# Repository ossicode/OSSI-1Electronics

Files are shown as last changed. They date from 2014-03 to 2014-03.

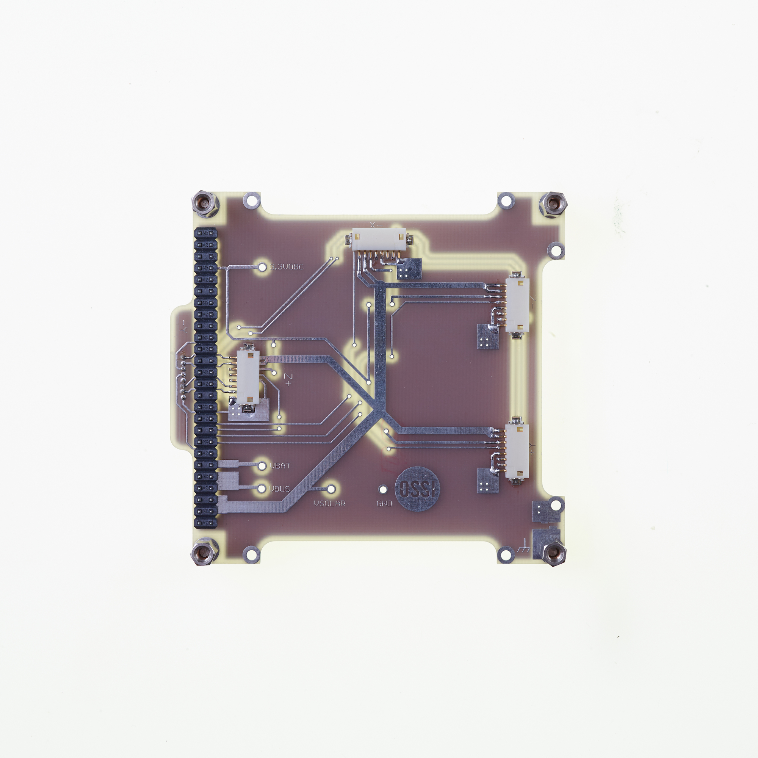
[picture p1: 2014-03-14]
OSSI-1 Interface Board/image/interface_T.jpg

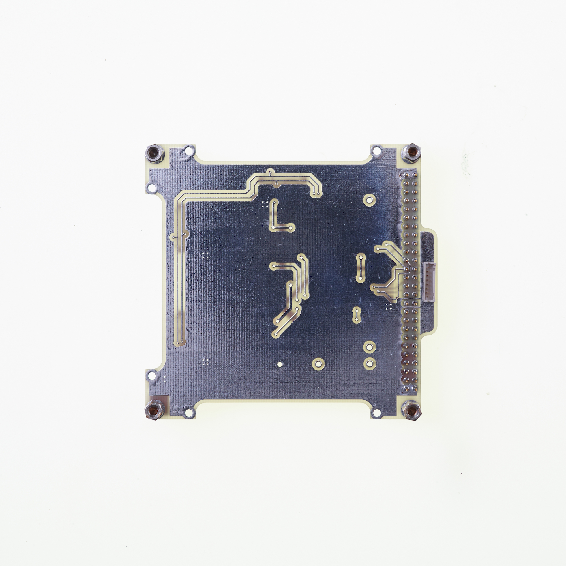
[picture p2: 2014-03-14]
OSSI-1 Interface Board/image/interface_B.jpeg

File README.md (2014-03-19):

### OSSI-1 Satellite Electronics Final Version 
#### Launched on 19th April 2013

**Check for modules for images, schematics, and BOMs.**

Mainly Eagle 6.1 / 6.5 version  
Please, see the comments from the schematic file for more information.  
Block diagram and rationale behind the design will be provided with video turorial soon.  

Open Source Satellite Initiative http://opensat.cc

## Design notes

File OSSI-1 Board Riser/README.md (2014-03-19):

### OSSI-1 Satellite Baord Riser

**Riser board to connect the signals between the battery board and the LED controller**

Mainly Eagle 6.1 / 6.5 version  
Please, see the comments from the schematic file for more information.  
Block diagram and rationale behind the design will be provided with video turorial soon.  

Open Source Satellite Initiative http://opensat.cc



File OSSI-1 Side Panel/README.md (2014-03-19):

### OSSI-1 Side Panel

**Solar panel for the sides.**  
**Temperature & current sensors are mounted on the panel for monitoring.**

Mainly Eagle 6.1 / 6.5 version  
Please, see the comments from the schematic file for more information.  
Block diagram and rationale behind the design will be provided with video turorial soon.  

Open Source Satellite Initiative http://opensat.cc



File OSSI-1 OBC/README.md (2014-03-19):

### OSSI-1 Satellite OBC Module

**The OBC is the mainboard of the satellite.**  
**The board checks the status of the satellite and makes decisions based on the data.**

Mainly Eagle 6.1 / 6.5 version  
Please, see the comments from the schematic file for more information.  
Block diagram and rationale behind the design will be provided with video turorial soon.  

Open Source Satellite Initiative http://opensat.cc



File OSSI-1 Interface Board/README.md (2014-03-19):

### OSSI-1 Satellite Interface Board

**The interface board is used to connect all solar paneles and deliver the power to the EPS.**  
**As the board is the the on the top, some signals can be measured for inspection.**

Mainly Eagle 6.1 / 6.5 version  
Please, see the comments from the schematic file for more information.  
Block diagram and rationale behind the design will be provided with video turorial soon.  

Open Source Satellite Initiative http://opensat.cc



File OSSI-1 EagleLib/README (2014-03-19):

Open Source Satellite Initiative Eagle CAD Library
http://opensat.cc

We used Eagle CAD 6.1 to design the board. Please, download one from:
http://www.cadsoftusa.com/downloads/

OSSI.lbr is the last version.

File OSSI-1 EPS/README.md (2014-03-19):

### OSSI-1 Satellite EPS

**EPS is the power supply board for the satellite.** 
**Multiple power sources are OR-ed by ideal diodes for reliabilty.**

Mainly Eagle 6.1 / 6.5 version  
Please, see the comments from the schematic file for more information.  
Block diagram and rationale behind the design will be provided with video turorial soon.  

Open Source Satellite Initiative http://opensat.cc



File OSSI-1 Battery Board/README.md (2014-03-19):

### OSSI-1 Satellite Battery Board

**The battery board contains Saft 144350 lithium-ion battery and two Nesscap supercapacitors.**  
**2 analog out temperature modules are attached to the battery and the supercapacitor for temp. monitoring.**

Mainly Eagle 6.1 / 6.5 version  
Please, see the comments from the schematic file for more information.  
Block diagram and rationale behind the design will be provided with video turorial soon.  

Open Source Satellite Initiative http://opensat.cc



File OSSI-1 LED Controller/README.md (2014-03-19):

### OSSI-1 Satellite LED Controller Module

**LED Controller Module is responsible for controlling 44W high power LEDs powered from supercapacitors.**  

Mainly Eagle 6.1 / 6.5 version  
Please, see the comments from the schematic file for more information.  
Block diagram and rationale behind the design will be provided with video turorial soon.  

Open Source Satellite Initiative http://opensat.cc



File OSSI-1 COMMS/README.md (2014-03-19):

### OSSI-1 Satellite COMMS

**Main communication system in OSSI-1.**  
**UHF RX/TX and TX is off by default to abide by the international rules.**

Mainly Eagle 6.1 / 6.5 version  
Please, see the comments from the schematic file for more information.  
Block diagram and rationale behind the design will be provided with video turorial soon.  

Open Source Satellite Initiative http://opensat.cc



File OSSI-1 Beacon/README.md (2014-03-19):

### OSSI-1 Satellite Beacon

**Beacon outputs 100mW VHF signas to transmit OSSI-1 satellite health data.**  
**Beacon transmits continuously.**

Mainly Eagle 6.1 / 6.5 version  
Please, see the comments from the schematic file for more information.  
Block diagram and rationale behind the design will be provided with video turorial soon.  

Open Source Satellite Initiative http://opensat.cc



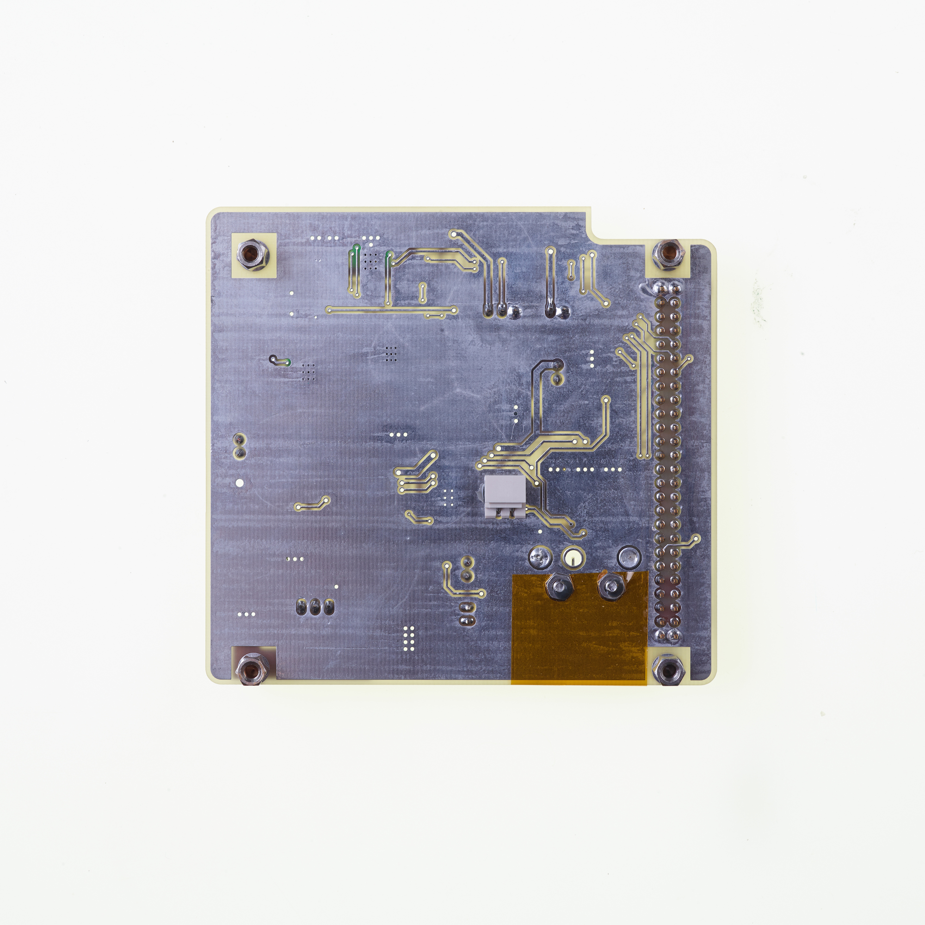
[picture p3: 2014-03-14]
OSSI-1 EPS/image/EPS_B.jpg

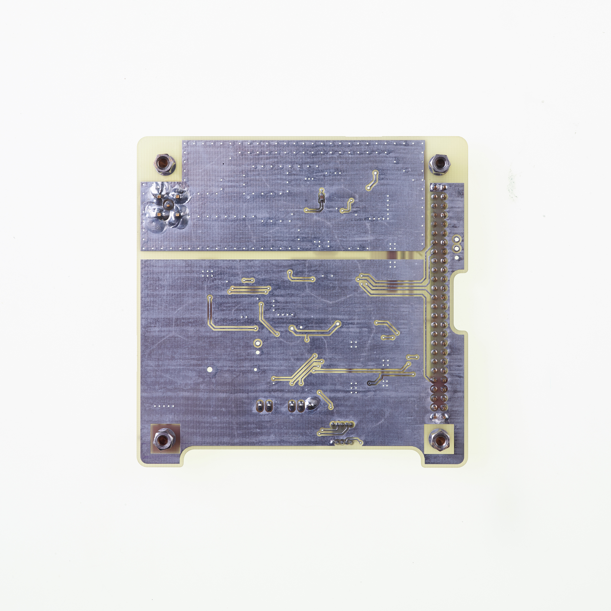
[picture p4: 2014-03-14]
OSSI-1 Beacon/image/Beacon_B.jpg

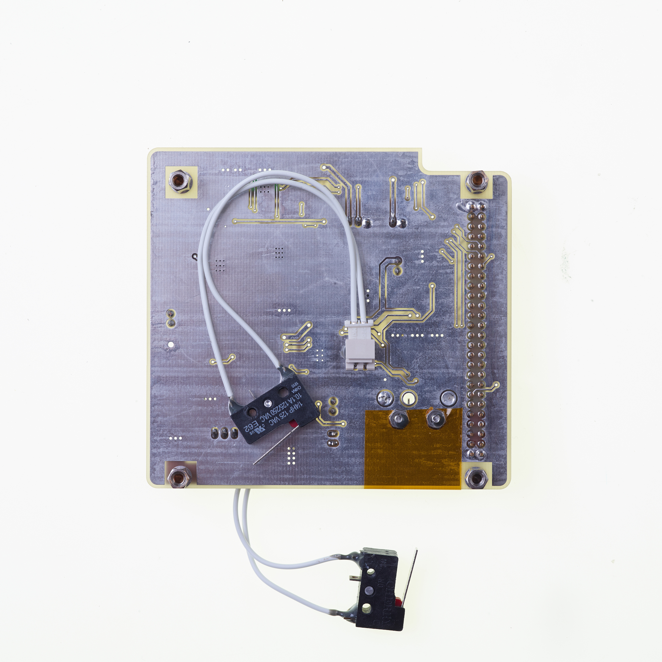
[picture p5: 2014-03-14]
OSSI-1 EPS/image/EPS_Switch_B.jpg

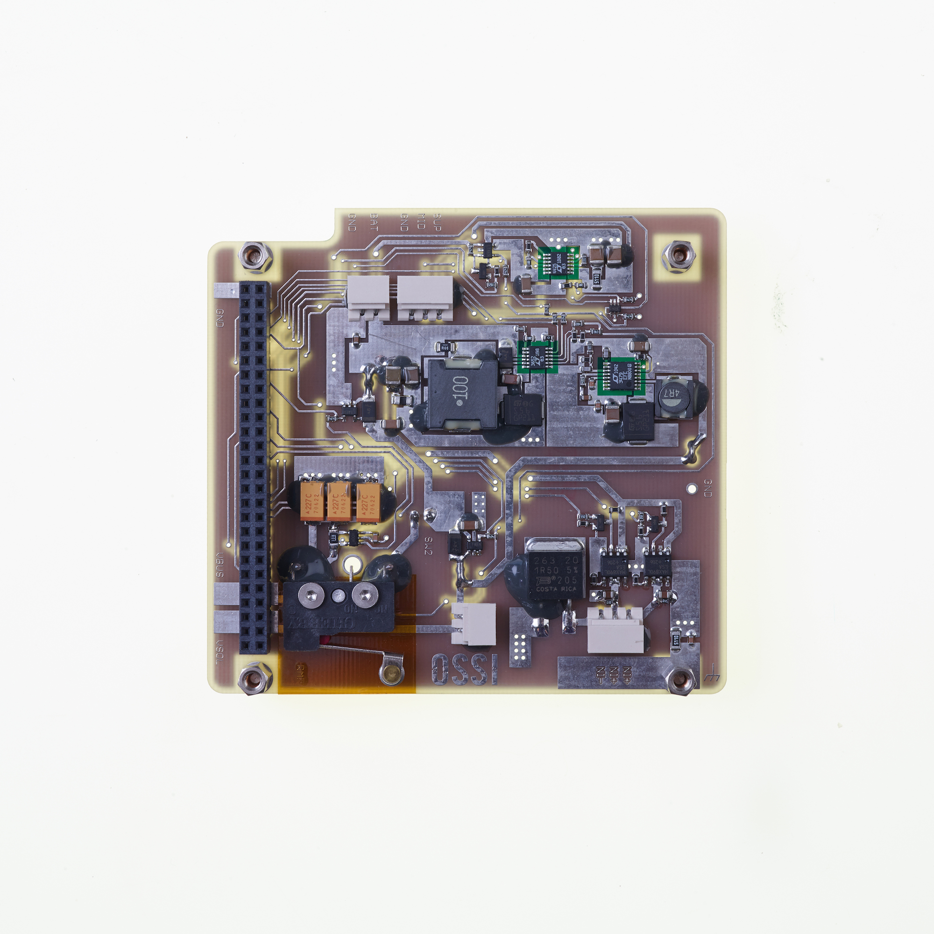
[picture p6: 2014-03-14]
OSSI-1 EPS/image/EPS_T.jpg

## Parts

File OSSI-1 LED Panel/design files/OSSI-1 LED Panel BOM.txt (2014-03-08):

Part	Value	Attributes	Package	Description	Part Num
LED1	LED-P7		P7		*
LED2	LED-P7		P7		*
LED3	LED-P7		P7		*
LED4	LED-P7		P7		*
X1	P-PAD		P-PAD		*
X2	P-PAD		P-PAD		*

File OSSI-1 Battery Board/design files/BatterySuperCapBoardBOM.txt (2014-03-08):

Part	Value	Attributes	Package	Description	Part Num
H1	MOUNT-PAD-ROUND3.2		3.2-PAD-ROUND		*
H2	MOUNT-PAD-ROUND3.2		3.2-PAD-ROUND		*
H3	MOUNT-PAD-ROUND3.2		3.2-PAD-ROUND		*
H4	MOUNT-PAD-ROUND3.2		3.2-PAD-ROUND		*
H5	MOUNT-PAD-ROUND3.2		3.2-PAD-ROUND		*
H6	MOUNT-PAD-ROUND3.2		3.2-PAD-ROUND		*
H7	MOUNT-PAD-ROUND3.2		3.2-PAD-ROUND		*
H8	MOUNT-PAD-ROUND3.2		3.2-PAD-ROUND		*
H9	MOUNT-PAD-ROUND3.2		3.2-PAD-ROUND		*
H10	MOUNT-PAD-ROUND3.2		3.2-PAD-ROUND		*
H11	MOUNT-PAD-ROUND3.2		3.2-PAD-ROUND		*
H12	MOUNT-PAD-ROUND3.2		3.2-PAD-ROUND		*
H13	MOUNT-PAD-ROUND3.2		3.2-PAD-ROUND		*
H14	MOUNT-PAD-ROUND3.2		3.2-PAD-ROUND		*
H15	MOUNT-PAD-ROUND3.2		3.2-PAD-ROUND		*
H16	MOUNT-PAD-ROUND3.2		3.2-PAD-ROUND		*
X1	ESQ-126-38-G-D		ESQ-126-XX-X-D	Samtec ESQ-126-XX-G-D Elevated Sockets Seires	*
X2	WEIDMULLER		WEIDMULLER1760490000		*
X3			1X03	Header 3	*
X4			1X03	Header 3	*

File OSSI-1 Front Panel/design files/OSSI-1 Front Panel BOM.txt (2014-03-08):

Part	Value	Attributes	Package	Description	Part Num
ADS1	OSSIADS		OSSIADS		*
C1	5.975pF		C0805(2012)		*
C2	5.975pF		C0805(2012)		*
L1	22.4nH		L0805(2012)		*
L2	22.4nH		L0805(2012)		*
L3	6mm dia, 5 turn		0207/10	INDUCTOR, American symbol	*
LD1	TEMT6000X01		TEMT6000-SEN	Ambient Light Sensor	*
R1	10k		R0805(2012)		*
X1	RFCON-MCX-V		MCX-V	RF Connectors	*
X2	RFCON-MCX-V		MCX-V	RF Connectors	*
X3	P-PAD-S		P-PAD-S		*
X4	P-PAD-S		P-PAD-S		*
X5	P-PAD-S		P-PAD-S		*
X6	P-PAD		P-PAD		*
X7	P-PAD		P-PAD		*
X8	P-PAD		P-PAD		*
X9	P-PAD		P-PAD		*
X10	P-PAD		P-PAD		*
X11	P-PAD-S		P-PAD-S		*

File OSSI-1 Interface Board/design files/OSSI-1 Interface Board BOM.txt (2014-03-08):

Part	Value	Attributes	Package	Description	Part Num
TP1	TP		TP-13		*
TP2	TP		TP-13		*
TP3	TP		TP-13		*
TP4	TP		TP-13		*
TP5	TP		TP-13		*
U$1	OSSILOGO-10		OSSILOGO1010		*
X1	ESQ-126-38-G-D		ESQ-126-XX-X-D	Samtec ESQ-126-XX-G-D Elevated Sockets Seires	*
C43	DNP		C0805(2012)		*
H1	MOUNT-PAD-ROUND3.2		3.2-PAD-ROUND		*
H2	MOUNT-PAD-ROUND3.2		3.2-PAD-ROUND		*
H3	MOUNT-PAD-ROUND3.2		3.2-PAD-ROUND		*
H4	MOUNT-PAD-ROUND3.2		3.2-PAD-ROUND		*
H5	MOUNT-PAD-ROUND2.1		2.1-PAD-ROUND		*
H6	MOUNT-PAD-ROUND2.1		2.1-PAD-ROUND		*
H9	MOUNT-PAD-ROUND2.1		2.1-PAD-ROUND		*
H10	MOUNT-PAD-ROUND2.1		2.1-PAD-ROUND		*
H11	MOUNT-PAD-ROUND2.1		2.1-PAD-ROUND		*
H12	MOUNT-PAD-ROUND2.1		2.1-PAD-ROUND		*
R39	DNP		WSL1206		*
X3	DF13DF13A-8P-1.25H		DF13A-8P	Hirose DF13 series connector	*
X4	DF13DF13-8P-1.25DSA		DF13-8P-1.25DSA	Hirose DF13 series connector	*
X6	DF13DF13A-8P-1.25H		DF13A-8P	Hirose DF13 series connector	*
X7	DF13DF13A-8P-1.25H		DF13A-8P	Hirose DF13 series connector	*
X8	DF13DF13A-8P-1.25H		DF13A-8P	Hirose DF13 series connector	*

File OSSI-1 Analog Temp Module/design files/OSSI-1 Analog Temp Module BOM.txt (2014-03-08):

Part	Value	Attributes	Package	Description	Part Num
C1	100nF		C0603(1608)		*
C2	100nF		C0603(1608)		*
JP1	JP2		JP2SMD0603		*
JP2	JP2		JP2SMD0603		*
U1	LM94022		SC70-5	LM94022 Temp Sensor From TI	*
X1	P-PAD-S		P-PAD-S		*
X2	P-PAD-S		P-PAD-S		*
X3	P-PAD-S		P-PAD-S		*

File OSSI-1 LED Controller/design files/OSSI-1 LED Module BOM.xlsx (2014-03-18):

Part | Value | Package | Description | Note | Manufacturer | Part Num | Order
C1 | DNP | C0805(2012)
H1 | MOUNT-PAD-ROUND3.2 | 3.2-PAD-ROUND
H2 | MOUNT-PAD-ROUND3.2 | 3.2-PAD-ROUND
H3 | MOUNT-PAD-ROUND3.2 | 3.2-PAD-ROUND
H4 | MOUNT-PAD-ROUND3.2 | 3.2-PAD-ROUND
R1 | DNP | WSL1206
X1 | ESQ-126-38-G-D | ESQ-126-XX-X-D | Samtec ESQ-126-XX-G-D Elevated Sockets Seires | Used by many satellites | Samtec | ESQ-126-38-G-D | Samtec.com
C2 | 12.5pF | C0603(1608)
C3 | 100nF | C0603(1608)
C4 | 12.5pF | C0603(1608)
C5 | 100nF | C0603(1608)
C6 | 100nF | C0603(1608)
C7 | 100nF | C0603(1608)
C8 | 100nF | C0603(1608)
C9 | 10uF, LDO Tantal 16V | C1206(3216)-A | TAJA105M020RNJ | Tantal Capacitor for LDO | Vishay Sprague | TR3A106K016C1700 | Digikey.com
C10 | 10uF, LDO Tantal 16V | C1206(3216)-A | TAJA105M020RNJ | Tantal Capacitor for LDO | Vishay Sprague | TR3A106K016C1700 | Digikey.com
C11 | 4.7uF, 1206 Cap | C1206-GCM31
C12 | 1uF | C0603(1608)
C13 | 100nF | C0603(1608)
C14 | 10uF, LDO Tantal 16V | C1206(3216)-A | TAJA105M020RNJ | Tantal Capacitor for LDO | Vishay Sprague | TR3A106K016C1700 | Digikey.com
C15 | 1uF 0805 | C0805(2012) |  | 35V, X7R | Murata | GCM21BR7YA105KA55L | Digikey.com
JP1 |  | JP1 | JUMPER
JP2 |  | JP1 | JUMPER
LED1 |  | LED-0603 | LEDs
LED2 |  | CHIPLED_0603 | LED
Q1 | NX-3215 | NX-3215 | NDK 32.768 kHz SMD Crystal | Automotive Grade | NDK | NX3215SA-32.768K-STD-MUS-2 | Digikey.com
R2 | 250 | R0603(1608)
R3 | 10k | R0603(1608)
R4 | 1k | R0603(1608)
R5 | 250 | R0603(1608)
R6 | 10k | R0603(1608)
R7 | 4.7k | R0603(1608)
R8 | 4.7k | R0603(1608)
R9 | 3k | R0603(1608)
R10 | 1k | R0603(1608)
R11 | 5.1k | R0603(1608)
R12 | 1k | R0603(1608)
R13 | 4.7k | R0603(1608)
R14 | 47k | R0603(1608)
R15 | 100k | R0603(1608)
R16 | DNP | R0603(1608)
R17 | 1k | R0603(1608)
R18 | 1.5k | R0603(1608)
R19 | 2.4k | R0603(1608)
R20 | 100k | R0603(1608)
R21 | 0.005, 2W RSENSE | R4527(12070) |  | High Power (2W) 1% Current Sense Resistor | Vishay Dale | WSR25L000FEA | element14.com
R22 | 1.1k | R0603(1608)
R23 | 1k | R0603(1608)
R24 | 100k | R0603(1608)
R25 | DNP | R0603(1608)
R26 | 1.5k | R0603(1608)
R27 | 0 | R0603(1608)
R28 | TBD | R0603(1608)
R29 | 100k | R0603(1608)
R30 | 100k | R0603(1608)
TP1 | TP | TP-13
TP2 | TP | TP-13
TP3 | TP | TP-13
TP4 | TP | TP-13
TP5 | TP | TP-13
TP6 | TP | TP-13
TP7 | TP | TP-13
TR1 | FDV301N | SOT23 | FDV301N Digital N channel - FET | Used sucessfully by swisscube | Fairchild Semiconductor | FDV301N | Digikey.com
TR2 | FDD8896 | TO252 | FDD8896 | 30V 94A N-Ch Mosfet for 9A pulse LED driving | Fairchild Semiconductor | FDD8896 | Digikey.com
U$ | OSSILOGORECT | OSSILOGORECT1005
U1 | MSP430F2132 | PW28 | *** MSP430F21x2 *** PW28 | high current rating | Texas Instruements | MSP430F2132TPWR | Digikey.com
U2 | OPA2347 | SOT23-8DCN | OPA2347 | op-amp | Texas Instruements | OPA2347EA/250 | Digikey.com
U3 | MAX4376 | SOT23-5DBV |  | Current Sensor, Gain = 50 | Maxim IC | MAX4376FAUK+T | Digikey.com
U4 | LM7321 | SO8 | LM7321 | op-amp used as mosfet driver | Texas Instruements | LM7321MA/NOPB | element14.com
U5 | MAX1682 | SOT23-5DBV | MAX1682EUK+T Charge Pump | Charge pump for lm7321 power | Maxim IC | MAX1682EUK+T | Digikey.com
U6 | TPS3838 | SOT23-5DBV | TPS3838 | IC Supervisor for relaible power-on | Texas Instruements | TPS3838K33QDBVRQ1 | Digikey.com
U7 | MAX890L | SO8 | MAX 890L | Current Limiter for SEU / SEL | Maxim IC | MAX890LESA+ | Digikey.com
U8 | MCP1700_SOT23 | SOT23 | MCP1700 LDO from Microchips | LDO used successfully by cubesats / External Capacitor is not that important compared to other LDO | Microchip | MCP1700T-3302E/TT | Digikey.com
X2 | 5268-03 | 5268-03
X3 |  | 1X03 | Header 3
X4 | 5268-03 | 5268-03
X5 | JTAG10PINMINI-H | M50-3200545 |  | Mini right angle 10-pin JTAG for MSP430 | Harwin Inc | M50-3200545 | Digikey.com
X6 | ICCON_POWERCON | ICCON6643220-1 |  | 35A rated power connector for led power | TE Connectivity | 6643220-1
X7 | ICCON_POWERCON | ICCON6643220-1 |  | 35A rated power connector for led power | TE Connectivity | 6643220-1
X8 | WEIDMULLER | WEIDMULLER1760490000 |  | 15A rated connector for led connection | Weidmuller | 1760490000
Unless noted othersie,_x000a_- Capacitors: GCM series from Murata / CGA series from TDK_x000a_- Resistors: ERJ 1% or 5% series from Panasonic Electronic Components_x000a__x000a_All all can be purchased from Digikey.com

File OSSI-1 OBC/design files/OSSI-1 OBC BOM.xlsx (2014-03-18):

Part | Value | Package | Description | Note | Manufacturer | Part Num | Order
H1 | MOUNT-PAD-ROUND3.2 | 3.2-PAD-ROUND
H2 | MOUNT-PAD-ROUND3.2 | 3.2-PAD-ROUND
H3 | MOUNT-PAD-ROUND3.2 | 3.2-PAD-ROUND
H4 | MOUNT-PAD-ROUND3.2 | 3.2-PAD-ROUND
X1 | ESQ-126-38-G-D | ESQ-126-XX-X-D | Samtec ESQ-126-XX-G-D Elevated Sockets Seires | Used by many satellites | Samtec | ESQ-126-37-G-D | Samtec.com
C1 | 100nF | C0603(1608)
C2 | 100nF | C0603(1608)
C3 | 100nF | C0603(1608)
C4 | 100nF | C0603(1608)
C5 | 100nF | C0603(1608)
C6 | 100nF | C0603(1608)
C7 | 100nF | C0603(1608)
C8 | 100nF | C0603(1608)
C9 | 100nF | C0603(1608)
C10 | 100nF | C0603(1608)
C11 | 100nF | C0603(1608)
C12 | 100nF | C0603(1608)
C13 | 100nF | C0603(1608)
C14 | 100nF | C0603(1608)
C15 | 100nF | C0603(1608)
C16 | 100nF | C0603(1608)
C17 | 100nF | C0603(1608)
R1 | 10k | R0603(1608)
R2 | 10k | R0603(1608)
R3 | 10k | R0603(1608)
R4 | 10k | R0603(1608)
R5 | 10k | R0603(1608)
R6 | 10k | R0603(1608)
R7 | 10k | R0603(1608)
R8 | 10k | R0603(1608)
R9 | 10k | R0603(1608)
R10 | 100k | R0603(1608)
R11 | 100k | R0603(1608)
R12 | 100k | R0603(1608)
R13 | 100k | R0603(1608)
R14 | 100k | R0603(1608)
R15 | 100k | R0603(1608)
R16 | 100k | R0603(1608)
R17 | 100k | R0603(1608)
R18 | 10k | R0603(1608)
U1 | OPA4347 | TSSOP14-PW | OPA4347 | op-amp | Texas Instruements | OPA4347EA/250 | Digikey.com
U2 | ADG708 | TSSOP16-RU |  | analog mux | Analog devices | ADG708CRUZ | Digikey.com
U3 | OPA4347 | TSSOP14-PW | OPA4347 | op-amp | Texas Instruements | OPA4347EA/250 | Digikey.com
U4 | ADR121 | TSOT-6UJ-6 | ADR127 | 2.5V reference | Analog devices | ADR121AUJZ-R2 | element14.com
U5 | ADG708 | TSSOP16-RU |  | analog mux | Analog devices | ADG708CRUZ | Digikey.com
U6 | OPA4347 | TSSOP14-PW | OPA4347 | op-amp | Texas Instruements | OPA4347EA/250 | Digikey.com
BAT1 | BATTERY-BH32T | BH32T-C-G |  | CR2032 battery holder | MPD (Memory Protection Devices) | BH32T-C-G | Digikey.com
C18 | 100nF | C0603(1608)
C19 | 100nF | C0603(1608)
C20 | 1uF 0805 | C0805(2012) |  | 35V, X7R | Murata | GCM21BR7YA105KA55L | Digikey.com
C21 | 100nF | C0603(1608)
C22 | 1uF 0805 | C0805(2012) |  | 35V, X7R | Murata | GCM21BR7YA105KA55L | Digikey.com
C23 | 1uF 0805 | C0805(2012) |  | 35V, X7R | Murata | GCM21BR7YA105KA55L | Digikey.com
C24 | 100nF | C0603(1608)
C25 | 100nF | C0603(1608)
C26 | 100nF | C0603(1608)
C27 | 100nF | C0603(1608)
C28 | 100nF | C0603(1608)
C29 | 4.7uF, 1210 | C1206-GCM31 |  | Ceramic 25V, X7R | Murata | GCM31CR71E475KA55L | Digikey.com
C30 | 10uF,3225 | C1210-GCM32 |  | 25V, X7R | Murata | GCM32ER71E106KA57L | Digikey.com
D1 | MMSD4148T1G | SOD-123 |  | switching diode for gyro | On Semi | MMSD4148T1G | Mouser.com
F1 | POLYSWITCH | NANOSMDC150FCT | Resettable Polyswitch | 1.5A Resettable Polyswitch fuse | TE Connectivity | NANOSMDC150F-2 | Digikey.com
L1 | 470uH, 240mA | L(2220) |  | inductor for gyro | Murata | LQH55DN471M03L | Mouser.com
R19 | 250 | R0603(1608)
R20 | 470k | R0603(1608)
R21 | 250 | R0603(1608)
R22 | 1.5k | R0603(1608)
R23 | 1.5k | R0603(1608)
R24 | 250 | R0603(1608)
R25 | 250 | R0603(1608)
R26 | 1.5k | R0603(1608)
R27 | 100k | R0603(1608)
R28 | 1.5k | R0603(1608)
R29 | 1.5k | R0603(1608)
R30 | 250 | R0603(1608)
R31 | 250 | R0603(1608)
R32 | 4.7k | R0603(1608)
R33 | 470k | R0603(1608)
R34 | 470k | R0603(1608)
R35 | 33k | R0603(1608)
R36 | 4.7k | R0603(1608)
R37 | 120, DNP | R0603(1608)
R38 | 250 | R0603(1608)
R39 | 4.7k | R0603(1608)
R40 | 33k | R0603(1608)
R41 | 250 | R0603(1608)
R42 | 4.7k | R0603(1608)
R43 | 470k | R0603(1608)
R44 | 4.7k | R0603(1608)
R45 | 100k | R0603(1608)
R46 | 470k | R0603(1608)
R47 | 100k | R0603(1608)
R48 | 100k | R0603(1608)
R49 | 100k | R0603(1608)
R50 | 1.5k | R0603(1608)
R51 | 1.5k | R0603(1608)
R52 | 1.5k | R0603(1608)
R53 | 1.5k | R0603(1608)
R54 | 10k | R0603(1608)
R55 | 1.5k | R0603(1608)
R56 | 1.5k | R0603(1608)
R57 | 1.5k | R0603(1608)
R58 | 10k | R0603(1608)
R59 | 10k | R0603(1608)
R60 | 10k | R0603(1608)
R61 | 10k | R0603(1608)
R62 | 100k | R0603(1608)
TR1 | FDV301N | SOT23 | FDV301N Digital N channel - FET | Used sucessfully by swisscube | Fairchild Semiconductor | FDV301N | Digikey.com
U7 | DS3231-L | SO16L | DS3231 | RTC | Maxim IC | DS3231SN# | element14.com
U8 | 24LC256-8LEAD | SO08-208 | 24LC256 | EEPROM | Microchip | 24LC256-E/SM | Mouser.com
U9 | LTC4411 | TSOT23-5 | Linear Techonology LTC4411 ideal diode | To power reset i2c ICs on OBC | Linear Technology | LTC4411ES5#TRMPBF | element14.com
U10 | ADXRS450SOIC | SOIC-16CAV |  | Gyro | Analog devices | ADXRS450BRGZ | Digikey.com
U11 | FM24V02-G | SO8 | FM24V02 | F-Ram | Ramtron | FM24V02-G | Mouser.com
U12 | TMP101 | SOT23-6DBV | TMP101 Digital Temerature Sensor with I2C Interface from Texas Instruments with Alert Function | i2c temp sensor with alarm | Texas Instruements | TMP101NA/3K | Digikey.com
U13 | SN65HVD11QD | SO8 | SN65HVD11 3.3V RS485 Transceiver | external interface | Texas Instruements | SN65HVD11QD | Mouser.com
U14 | TCA9548APWR | TSSOP-24-PW | TCA9548APWR | I2C switch | Texas Instruements | TCA9548APWR | Digikey.com
U15 | SN74LVC8T245PWR | PW_R-PDSO-G24 | SN74LVC8T245 | io protection buffer | Texas Instruements | SN74LVC8T245PWR | Mouser.com
U16 | LTC4411 | TSOT23-5 | Linear Techonology LTC4411 ideal diode | To bypass external power to satellite | Linear Technology | LTC4411ES5#TRMPBF | element14.com
X2 | MOLEX-22-05-7045 | 22-05-7045 | molex spoxt 5268 series 22-05-7045 for external interface
C31 | 12.5pF | C0603(1608)
C32 | 12.5pF | C0603(1608)
C33 | 100nF | C0603(1608)
C34 | 100nF | C0603(1608)
C35 | 100nF | C0603(1608)
C36 | 100nF | C0603(1608)
C37 | 100nF | C0603(1608)
C38 | 1uF | C0603(1608)
C39 | 100nF | C0603(1608)
C40 | 10uF, LDO Tantal 16V | C1206(3216)-A | TAJA105M020RNJ | Tantal Capacitor for LDO | Vishay Sprague | TR3A106K016C1700 | Digikey.com
C41 | 10uF, LDO Tantal 16V | C1206(3216)-A | TAJA105M020RNJ | Tantal Capacitor for LDO | Vishay Sprague | TR3A106K016C1700 | Digikey.com
JP1 |  | JP1 | JUMPER
LED1 |  | LED-0603 | LEDs
Q1 | NX-3215 | NX-3215 | NDK 32.768 kHz SMD Crystal | Automotive Grade | NDK | NX3215SA-32.768K-STD-MUS-2 | Digikey.com
R63 | 250 | R0603(1608)
R64 | 250 | R0603(1608)
R65 | 10k | R0603(1608)
R66 | 300k | R0603(1608)
R67 | 10k | R0603(1608)
R68 | 4.7k | R0603(1608)
R69 | 4.7k | R0603(1608)
R70 | 4.7k | R0603(1608)
R71 | 4.7k | R0603(1608)
R72 | 0 | R0603(1608)
R73 | 0 | R0603(1608)
R74 | 6.2k | R0603(1608)
R75 | 0 | R0603(1608)
R76 | 100k | R0603(1608)
R77 | 100k | R0603(1608)
U$1 | OSSILOGORECT | OSSILOGORECT1005
U17 | MSP430F1611 | PM/PAG64 | MSP430F1611 | Used by many cubesats / I2C issue in the chip / MSP430F2618 is better choice | Texas Instruements | MSP430F1611IPMR | Digikey.com
U18 | MAX6369 | SOT23-8 | MAX6369 | External Watchdog timer | Maxim IC | MAX6369KA+T | Digikey.com
U19 | TPS3838 | SOT23-5DBV | TPS3838 | IC Supervisor for relaible power-on | Texas Instruements | TPS3838K33QDBVRQ1 | Digikey.com
U20 | MAX890L | SO8 | MAX 890L | Current Limiter for SEU / SEL | Maxim IC | MAX890LESA+ | Digikey.com
U21 | MCP1700_SOT23 | SOT23 | MCP1700 LDO from Microchips | LDO used successfully by cubesats / External Capacitor is not that important compared to other LDO | Microchip | MCP1700T-3302E/TT | Digikey.com
X3 |  | 1X03 | Header 3
X4 | P-PAD-S | P-PAD-S
X5 | P-PAD-S | P-PAD-S
X6 | JTAG10PINMINI-H | M50-3200545 |  | Mini right angle 10-pin JTAG for MSP430 | Harwin Inc | M50-3200545 | Digikey.com
Unless noted othersie,_x000a_- Capacitors: GCM series from Murata / CGA series from TDK_x000a_- Resistors: ERJ 1% or 5% series from Panasonic Electronic Components_x000a__x000a_All all can be purchased from Digikey.com

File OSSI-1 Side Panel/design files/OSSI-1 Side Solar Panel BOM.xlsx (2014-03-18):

Part | Value | Package | Description | Note | Manufacturer | Part Num | Order
C1 | 100nF | C0603(1608)
D1 | STPS0520Z | SOD-123 | We use STPS0520Z by st.com diode for solar cell schottky diode. | schottky diode for reverse current blocking | STMicroelectronics | STPS0520Z | Digikey.com
D2 | STPS0520Z | SOD-123 | We use STPS0520Z by st.com diode for solar cell schottky diode.
D3 | STPS0520Z | SOD-123 | We use STPS0520Z by st.com diode for solar cell schottky diode.
D4 | STPS0520Z | SOD-123 | We use STPS0520Z by st.com diode for solar cell schottky diode.
D5 | STPS0520Z | SOD-123 | We use STPS0520Z by st.com diode for solar cell schottky diode.
D6 | STPS0520Z | SOD-123 | We use STPS0520Z by st.com diode for solar cell schottky diode.
D7 | STPS0520Z | SOD-123 | We use STPS0520Z by st.com diode for solar cell schottky diode.
D8 | STPS0520Z | SOD-123 | We use STPS0520Z by st.com diode for solar cell schottky diode.
D9 | STPS0520Z | SOD-123 | We use STPS0520Z by st.com diode for solar cell schottky diode.
D10 | STPS0520Z | SOD-123 | We use STPS0520Z by st.com diode for solar cell schottky diode.
D11 | STPS0520Z | SOD-123 | We use STPS0520Z by st.com diode for solar cell schottky diode.
D12 | STPS0520Z | SOD-123 | We use STPS0520Z by st.com diode for solar cell schottky diode.
H1 | MOUNT-PAD-ROUND2.1 | 2.1-PAD-ROUND
H2 | MOUNT-PAD-ROUND2.1 | 2.1-PAD-ROUND
H3 | MOUNT-PAD-ROUND2.1 | 2.1-PAD-ROUND
H4 | MOUNT-PAD-ROUND2.1 | 2.1-PAD-ROUND
JP1 | JP2 | JP2SMD0603 |  | set i2c address for tmp100
JP2 | JP2 | JP2SMD0603 |  | set i2c address for tmp100
R1 | 250 | R0603(1608)
R2 | 250 | R0603(1608)
R3 | 50m | WSL1206 |  | 1% current sense resistor | Vishay Dale | WSL1206R0500FEA18 | Digikey.com
R4 | 1k | R0603(1608)
S1 | TASCSOLARCELL | TASCSOLARCELL |  | Hard to get / Hard to mount / Used by many cubesats / Epo-Tek H20E silver epoxy is used for mounting | Spectrolab | TASC Solar Cell | spectrolab.com/‎
S2 | TASCSOLARCELL | TASCSOLARCELL
S3 | TASCSOLARCELL | TASCSOLARCELL
S4 | TASCSOLARCELL | TASCSOLARCELL
S5 | TASCSOLARCELL | TASCSOLARCELL
S6 | TASCSOLARCELL | TASCSOLARCELL
S7 | TASCSOLARCELL | TASCSOLARCELL
S8 | TASCSOLARCELL | TASCSOLARCELL
S9 | TASCSOLARCELL | TASCSOLARCELL
S10 | TASCSOLARCELL | TASCSOLARCELL
S11 | TASCSOLARCELL | TASCSOLARCELL
S12 | TASCSOLARCELL | TASCSOLARCELL
S13 | TASCSOLARCELL | TASCSOLARCELL
S14 | TASCSOLARCELL | TASCSOLARCELL
S15 | TASCSOLARCELL | TASCSOLARCELL
S16 | TASCSOLARCELL | TASCSOLARCELL
S17 | TASCSOLARCELL | TASCSOLARCELL
S18 | TASCSOLARCELL | TASCSOLARCELL
S19 | TASCSOLARCELL | TASCSOLARCELL
S20 | TASCSOLARCELL | TASCSOLARCELL
S21 | TASCSOLARCELL | TASCSOLARCELL
S22 | TASCSOLARCELL | TASCSOLARCELL
S23 | TASCSOLARCELL | TASCSOLARCELL
S24 | TASCSOLARCELL | TASCSOLARCELL
U$2 | OSSILOGO | OSSILOGORECT1005
U1 | TMP100 | SOT23-6DBV | TMP100 Digital Temerature Sensor with I2C Interface from Texas Instruments | I2C Temp sensor | Texas Instruements | TMP100NA/3K | Digikey.com
U2 | MAX4376 | SOT23-5DBV |  | Current Sensor, Gain = 50 | Maxim IC | MAX4376FAUK+T | Digikey.com
X1 | DF13DF13A-8P-1.25H | DF13A-8P | Hirose DF13 series connector | 1.25mm pitch |  | DF13A-8P-1.25H(50) | Digikey.com
Unless noted othersie,_x000a_- Capacitors: GCM series from Murata / CGA series from TDK_x000a_- Resistors: ERJ 1% or 5% series from Panasonic Electronic Components_x000a__x000a_All all can be purchased from Digikey.com

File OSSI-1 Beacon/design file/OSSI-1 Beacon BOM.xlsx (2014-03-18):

Part | Value | Package | Description | Note | Manufacturer | Part Num | Order
C1 | DNP | C0805(2012)
H1 | MOUNT-PAD-ROUND3.2 | 3.2-PAD-ROUND
H2 | MOUNT-PAD-ROUND3.2 | 3.2-PAD-ROUND
H3 | MOUNT-PAD-ROUND3.2 | 3.2-PAD-ROUND
H4 | MOUNT-PAD-ROUND3.2 | 3.2-PAD-ROUND
R1 | DNP | WSL1206
X1 | P-PAD-S | P-PAD-S
X2 | ESQ-126-38-G-D | ESQ-126-XX-X-D | Samtec ESQ-126-XX-G-D Elevated Sockets Seires | Used by many satellites | Samtec | ESQ-126-38-G-D | Samtec.com
X3 | P-PAD-S | P-PAD-S
C2 | 10nF | C0603(1608)
C3 | 10nF | C0603(1608)
C4 | 0R | C0603(1608)
C5 | 10nF | C0603(1608)
C6 | 100nF | C0603(1608)
C7 | 1uF,0805 | C0805(2012) |  | 35V, X7R | Murata | GCM21BR7YA105KA55L | Digikey.com
C8 | 22uF,1210 | C1210-GCM32 |  | Ceramic 25V, X7R | Taiyo Yuden | TMK325B7226MM-TR | Digikey.com
C9 | 1uF | C0603(1608)
C10 | 100nF | C0603(1608)
F1 | LFCN-160 | LFCN | LFCN-160 Low Pass Filter |  | Mini-Circuits | LFCN-160+ | http://www.minicircuits.com/
L1 | 470nH, 1008 size | L1008(2520) |  | Important for impedance matching | Coilcraft | 1008HT-R47TJL | Coilcraft.com
R2 | 100k | R0603(1608)
R3 | 6.2k | R0603(1608)
R4 | 100k | R0603(1608)
R5 | 100k | R0603(1608)
TR1 | FDV301N | SOT23 | FDV301N Digital N channel - FET | Used sucessfully by swisscube | Fairchild Semiconductor | FDV301N | Digikey.com
U1 | ADL5530 | LFCSP8_CP | ADL5530 |  | analog devices
U2 | MAX890L | SO8 | MAX 890L | Current Limiter for SEU / SEL | Maxim IC | MAX890LESA+ | Digikey.com
X4 | RFCON-MCX-R/A | MCX-R/A | RF Connectors
C11 | 22pF | C0603(1608) |  | RF Filter
C12 | 39pF | C0603(1608) |  | RF Filter
C13 | 22pF | C0603(1608) |  | RF Filter
C14 | 1nF | C0603(1608)
C15 | 10nF | C0603(1608)
C16 | 1nF | C0603(1608)
C17 | 2.2uF, 0805 | C0805(2012)
C18 | 100pF | C0603(1608)
C19 | 1uF | C0603(1608)
C20 | 1uF,0603 Too Small!! | C0603(1608)
C21 | DNP | C0603(1608)
C22 | 100pF | C0603(1608)
C23 | 1uF 0805 | C0805(2012)
C24 | 1uF,0603 | C0603(1608)
C25 | 22nF | C0603(1608)
C26 | 68pF | C0603(1608)
C27 | 1000pF | C0603(1608)
C28 | 22pF | C0603(1608)
L2 | 68nH | L0603(1608) |  | RF Filter | Coilcraft | 0603HP-68NXJLU | Coilcraft.com
L3 | 68nH | L0603(1608) |  | RF Filter | Coilcraft | 0603HP-68NXJLU | Coilcraft.com
L4 | 8.2nH | L0603(1608) |  | Very Important For PLL Lock, tune this value for more PLL lock margin | Coilcraft | 0603HP-8N2XJE | Coilcraft.com
L5 | 470nH, 1008 size | L1008(2520) |  | Important for impedance matching | Coilcraft | 1008HT-R47TJL | Coilcraft.com
R6 | 0 | R0603(1608)
R7 | 1M | R0603(1608)
R8 | 3.6k | R0603(1608)
R9 | 2.4k | R0603(1608)
R10 | 5.1k | R0603(1608)
TCXO1 | 19.2MHz | TCXO_M532 | 532L25DT19M2000: CTO electronic components Model 532 19.2MHz TCXO for RF transeiver |  | CTO electronic components | 532L25DT19M2000 | Digikey.com
U3 | NC7SZ04 | SC70-5 | UHS Inverter NC7SZ04 | To convert the output of TCXO from clipped sinewave to CMOS level | Fairchild | NC7SZ04P5X | Mouser.com
U4 | ADF7012 | TSSOP24 |  | Used successfully by many cubesats as VHF beacon / Hard to buy | analog devices | ADF7012BRUZ | element14.com
C29 | 100nF | C0603(1608)
C30 | TBD | C0603(1608)
C31 | 100nF | C0603(1608)
C32 | 12.5pF | C0603(1608)
C33 | 100nF | C0603(1608)
C34 | 12.5pF | C0603(1608)
C35 | 100nF | C0603(1608)
C36 | 100nF | C0603(1608)
C37 | 1uF | C0603(1608)
C38 | 100nF | C0603(1608)
C39 | 10uF, LDO Tantal 16V | C1206(3216)-A | TAJA105M020RNJ | Tantal Capacitor for LDO | Vishay Sprague | TR3A106K016C1700 | Digikey.com
C40 | 10uF, LDO Tantal 16V | C1206(3216)-A | TAJA105M020RNJ | Tantal Capacitor for LDO | Vishay Sprague | TR3A106K016C1700 | Digikey.com
C41 | 10nF | C0603(1608)
C42 | 22uF,1210 | C1210-GCM32 |  | Ceramic 25V, X7R | Taiyo Yuden | TMK325B7226MM-TR | Digikey.com
C43 | 100nF | C0603(1608)
D1 | BAT54S | SOT23 | Schottky Diodes | Switch ESD protection | STMicroelectronics | BAT54SFILM | Digikey.com
JP1 |  | JP1 | JUMPER
L6 | 7 R Ferrite Bead, 3A | L0805(2012) |  | 7 Ohm 3A Ferrite Bead for pi filter | Wurth Electronics Inc | 742792010 | Digikey.com
LED1 |  | LED-0603 | LEDs
Q1 | NX-3215 | NX-3215 | NDK 32.768 kHz SMD Crystal | Automotive Grade | NDK | NX3215SA-32.768K-STD-MUS-2 | Digikey.com
R11 | 47k | R0603(1608)
R12 | 4.7k | R0603(1608)
R13 | 250 | R0603(1608)
R14 | 10k | R0603(1608)
R15 | 1k | R0603(1608)
R16 | 250 | R0603(1608)
R17 | 100k | R0603(1608)
R18 | 10k | R0603(1608)
R19 | 4.7k | R0603(1608)
R20 | 4.7k | R0603(1608)
R21 | 100k | R0603(1608)
R22 | 4.7k | R0603(1608)
R23 | 4.7k | R0603(1608)
R24 | 4.7k | R0603(1608)
R25 | 4.7k | R0603(1608)
R26 | 4.7k | R0603(1608)
R27 | 4.7k | R0603(1608)
R28 | 4.7k | R0603(1608)
R29 | DNP | R0603(1608)
R30 | 10k | R0603(1608)
R31 | 4.7k | R0603(1608)
R32 | 100k | R0603(1608)
R33 | 0 | R0603(1608)
R34 | 23.7k | R0603(1608)
R35 | 100k | R0603(1608)
R36 | 100k | R0603(1608)
TP1 | TP | TP-13
U$1 | OSSILOGORECT | OSSILOGORECT1005
U5 | MAX6369 | SOT23-8 | MAX6369 | External Watchdog timer | Maxim IC | MAX6369KA+T | Digikey.com
U6 | MSP430F2132 | PW28 | *** MSP430F21x2 *** PW28 | high current rating | Texas Instruements | MSP430F2132TPWR | Digikey.com
U7 | OPA2347 | SOT23-8DCN | OPA2347 | op-amp | Texas Instruements | OPA2347EA/250 | Digikey.com
U8 | TPS3838 | SOT23-5DBV | TPS3838 | IC Supervisor for relaible power-on | Texas Instruements | TPS3838K33QDBVRQ1 | Digikey.com
U9 | MAX890L | SO8 | MAX 890L | Current Limiter for SEU / SEL | Maxim IC | MAX890LESA+ | Digikey.com
U10 | MCP1700_SOT23 | SOT23 | MCP1700 LDO from Microchips | LDO used successfully by cubesats / External Capacitor is not that important compared to other LDO | Microchip | MCP1700T-3302E/TT | Digikey.com
X5 | 5268-02 | 5628-02
X6 |  | 1X03 | Header 3
X7 | 5268-03 | 5268-03
X8 | JTAG10PINMINI-H | M50-3200545 |  | Mini right angle 10-pin JTAG for MSP430 | Harwin Inc | M50-3200545 | Digikey.com
Unless noted othersie,_x000a_- Capacitors: GCM series from Murata / CGA series from TDK_x000a_- Resistors: ERJ 1% or 5% series from Panasonic Electronic Components_x000a__x000a_All all can be purchased from Digikey.com

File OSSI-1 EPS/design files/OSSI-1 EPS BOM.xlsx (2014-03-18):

Part | Value | Package | Description | Note | Manufacturer | Part Num | Order
C1 | 100nF | C0805(2012)
H1 | MOUNT-PAD-ROUND3.2 | 3.2-PAD-ROUND
H2 | MOUNT-PAD-ROUND3.2 | 3.2-PAD-ROUND
H3 | MOUNT-PAD-ROUND3.2 | 3.2-PAD-ROUND
H4 | MOUNT-PAD-ROUND3.2 | 3.2-PAD-ROUND
R1 | 511 | WSL1206 |  | Chassis ESD shock absorbing resistor | Panasonic | ERJ-8ENF5110V | Digikey.com
TP1 | TP | TP-13
X1 | ESQ-126-38-G-D | ESQ-126-XX-X-D | Samtec ESQ-126-XX-G-D Elevated Sockets Seires | Used by many satellites | Samtec | ESQ-126-38-G-D | Samtec.com
C2 | 1uF, 0805 | C0805(2012) |  | 35V, X7R | Murata | GCM21BR7YA105KA55L | Digikey.com
C3 | 1uF, 0805 | C0805(2012) |  | 35V, X7R | Murata | GCM21BR7YA105KA55L | Digikey.com
R2 | 100k | R0603(1608)
R3 | 1.5k | R0603(1608)
R4 | 1.2k | R0603(1608)
R5 | 1R5, 20W, 1% | PWR263S-20 |  | 1.5 Ohm 20Watt small SMT resistor for nichrome wire cutting | Bourns Inc. | PWR263S-20-1R50J | Digikey.com
R6 | 100k | R0603(1608)
R7 | 1.2k | R0603(1608)
R8 | 1.5k | R0603(1608)
R9 | 100k | R0603(1608)
R10 | 100k | R0603(1608)
R41 | 1M | R0603(1608)
R42 | 1M | R0603(1608)
TR1 | FDV301N | SOT23 | FDV301N Digital N channel - FET | Used sucessfully by swisscube | Fairchild Semiconductor | FDV301N | Digikey.com
TR2 | FDV301N | SOT23 | FDV301N Digital N channel - FET | Used sucessfully by swisscube | Fairchild Semiconductor | FDV301N | Digikey.com
U1 | MAX890L | SO8 | MAX 890L | Current Limiter for SEU / SEL | Maxim IC | MAX890LESA+ | Digikey.com
U2 | MAX890L | SO8 | MAX 890L | Current Limiter for SEU / SEL | Maxim IC | MAX890LESA+ | Digikey.com
X2 | 5268-03 | 5268-03 |  | Molex 2.54 pitch 3pin Right Angle | Molex
C4 | 2.2uF | C1206-GCM31 |  | Ceramic 50V, X7R | Murata | GCM31CR71H225KA55L | Digikey.com
C5 | 22uF | C1210-GCM32 |  | Ceramic 25V, X7R | Taiyo Yuden | TMK325B7226MM-TR | Digikey.com
C6 | 22uF | C1210-GCM32 |  | Ceramic 25V, X7R | Taiyo Yuden | TMK325B7226MM-TR | Digikey.com
C7 | 100pF | C0603(1608)
C8 | 2.2uF | C1206-GCM31 |  | Ceramic 50V, X7R | Murata | GCM31CR71H225KA55L | Digikey.com
C9 | 4.7uF, 1206 | C1206-GCM31 |  | Ceramic 25V, X7R | Murata | GCM31CR71E475KA55L | Digikey.com
C10 | 0 Ohm | C0603(1608)
C11 | 22nF | C0603(1608)
C12 | 220uF | C2917(7343)-Y | TAJY227K010RNJ | The crucial capacitor for the satellite power system. If this fails, system fails. Ref:swisscube / Tantal 10V | AVX | TAJY227K010RNJ | Digikey.com
C13 | 220uF | C2917(7343)-Y | TAJY227K010RNJ |  | AVX | TAJY227K010RNJ | Digikey.com
C14 | 220uF | C2917(7343)-Y | TAJY227K010RNJ |  | AVX | TAJY227K010RNJ | Digikey.com
C15 | 0.1uF | C0603(1608)
C16 | 100uF | C1210-TMK325 |  | Ceramic 25V, X7R | Taiyo Yuden | EMK325ABJ107MM-T | Digikey.com
C17 | 10uF | C1210-GCM32 |  | 25V, X7R | Murata | GCM32ER71E106KA57L | Digikey.com
C18 | 10nF | C0603(1608)
C19 | 470pF | C0603(1608)
C20 | 0.1uF | C0603(1608)
C21 | 10uF | C1210-GCM32 |  | 25V, X7R | Murata | GCM32ER71E106KA57L | Digikey.com
C22 | 1uF, 100V, 1206 | C0805(2012) |  | 100V, X7R | TDK | CGA5L2X7R2A105K160AA | Digikey.com
C23 | 0.1uF | C0603(1608)
C24 | 4.7uF, 1206 | C1206-GCM31 |  | Ceramic 25V, X7R | Murata | GCM31CR71E475KA55L | Digikey.com
D1 | PMEG6020EP | PMEG6020EP |  | Schottky 60V 2A | NXP Semiconductors | PMEG6020EP,115 | Digikey.com
D2 | STPS5L60 | STPS5L60 | STPS5L60 | Schottky 60V 5A | STMicroelectronics | STPS5L60S | Digikey.com
D3 | STPS5L60 | STPS5L60 | STPS5L60 | Schottky 60V 5A | STMicroelectronics | STPS5L60S | Digikey.com
D4 | PMEG3050BEP | PMEG6020EP |  | Schottky 30V 5A | NXP Semiconductors | PMEG3050BEP,115 | Digikey.com
D5 | PMEG3050BEP | PMEG6020EP |  | Schottky 30V 5A | NXP Semiconductors | PMEG3050BEP,115 | Digikey.com
JP1 |  | JP1 | JUMPER
JP2 |  | JP1 | JUMPER
JP3 |  | JP1 | JUMPER
L1 | 4.7uH | RLF7030 |  | high current SMD Inductor | TDK | RLF7030T-4R7M3R4 | Mouser.com
L2 | 10uH | RLF12545 |  | high current SMD Inductor | TDK | RLF12545T-100M5R1-PF | Mouser.com
R11 | 100k | R0603(1608)
R12 | 1.5k | R0603(1608)
R13 | 470k | R0603(1608)
R14 | 511 | WSL1206 |  | 0.01 | Panasonic | ERJ-8ENF5110V | Digikey.com
R15 | 470k | R0603(1608)
R16 | 750k | R0603(1608)
R17 | 1.5M | R0603(1608)
R18 | 2k | R0603(1608)
R19 | 470k | R0603(1608)
R20 | 1.5M | R0603(1608)
R21 | 750k | R0603(1608)
R22 | 470k | R0603(1608)
R23 | 470k | R0603(1608)
R24 | 17.8k | R0603(1608)
R25 | 30.9k | R0603(1608)
R26 | 0.1 | WSL1206 |  | 1% current sense resistor | Panasonic | ERJ-8BWFR100V | Digikey.com
R27 | 169k | R0603(1608)
R28 | 100k | R0603(1608)
R29 | 100k | R0603(1608)
R30 | 1.5M | R0603(1608)
R31 | 4.3k | R0603(1608)
R32 | 300k | R0603(1608)
R33 | 200k | R0603(1608)
R34 | 36k | R0603(1608)
R35 | 10m | WSL1206
R36 | 0.05 | WSL1206 |  | 1% current sense resistor | Vishay Dale | WSL1206R0500FEA18 | Digikey.com
R37 | 470k | R0603(1608)
R38 | 470k | R0603(1608)
R39 | 470k | R0603(1608)
R40 | 470k | R0603(1608)
TR3 | FDV301N | SOT23 | FDV301N Digital N channel - FET | Used sucessfully by swisscube | Fairchild Semiconductor | FDV301N | Digikey.com
U$1 | OSSILOGORECT | OSSILOGORECT1005
U3 | LTC4411 | TSOT23-5 | Linear Techonology LTC4411 ideal diode | FET based Ideal diode to turn on/off supercap charger | Linear Technology | LTC4411ES5#TRMPBF | element14.com
U4 | LTC4425 | MSE | LTC4425 Linear SuperCap Charger With Current-Limited Ideal Diode and V/I Monitor |  | Linear Technology | LTC4425EMSE#PBF | Digikey.com
U5 | SN74LVC1T45-EP | SOT-6DCK | SN74LVC1T45-EP | To proejct supercap charger when system power resets | Texas Instruments | SN74LVC1T45MDCKREP
U6 | 3479 | TSSOP16-FE | LT3479 inverting switching convertor |  | Linear Technology | LT3479EFE#PBF | Digikey.com
U7 | LTC4411 | TSOT23-5 | Linear Techonology LTC4411 ideal diode | FET based Ideal diode for lower drop power OR-ing | Linear Technology | LTC4411ES5#TRMPBF | element14.com
U8 | 3652 | MSE | LT3652 Battery Charger |  | Linear Technology | LT3652EMSE#PBF | Digikey.com
U9 | MAX4376 | SOT23-5DBV |  | Current Sensor, Gain = 50 | Maxim IC | MAX4376FAUK+T | Digikey.com
U10 | LTC4411 | TSOT23-5 | Linear Techonology LTC4411 ideal diode | FET based Ideal diode for lower drop power OR-ing | Linear Technology | LTC4411ES5#TRMPBF | element14.com
X3 | 5268-03 | 5268-03
X4 | 5268-02 | 5628-02
X5 | 5268-02 | 5628-02
X6 | E62-10K | E62-10K | Cherry E620-10K spdt sw for Remove Before Flight pin | power switch used my many cubesats | Cherry | E62-10K | Digikey.com
X7 | 5268-02 | 5628-02
Unless noted othersie,_x000a_- Capacitors: GCM series from Murata / CGA series from TDK_x000a_- Resistors: ERJ 1% or 5% series from Panasonic Electronic Components_x000a__x000a_All all can be purchased from Digikey.com
/ EPS used many 1% reistors for voltage feedback

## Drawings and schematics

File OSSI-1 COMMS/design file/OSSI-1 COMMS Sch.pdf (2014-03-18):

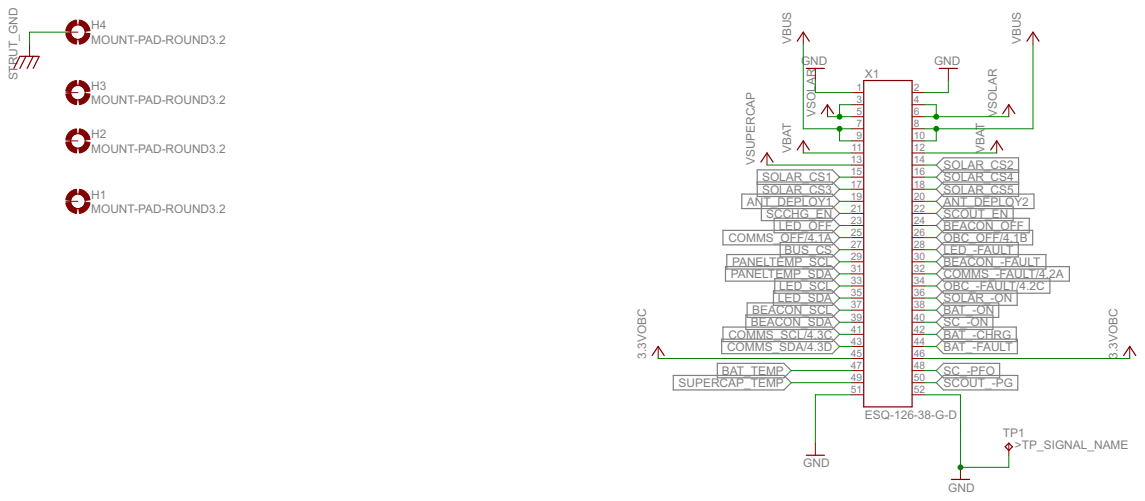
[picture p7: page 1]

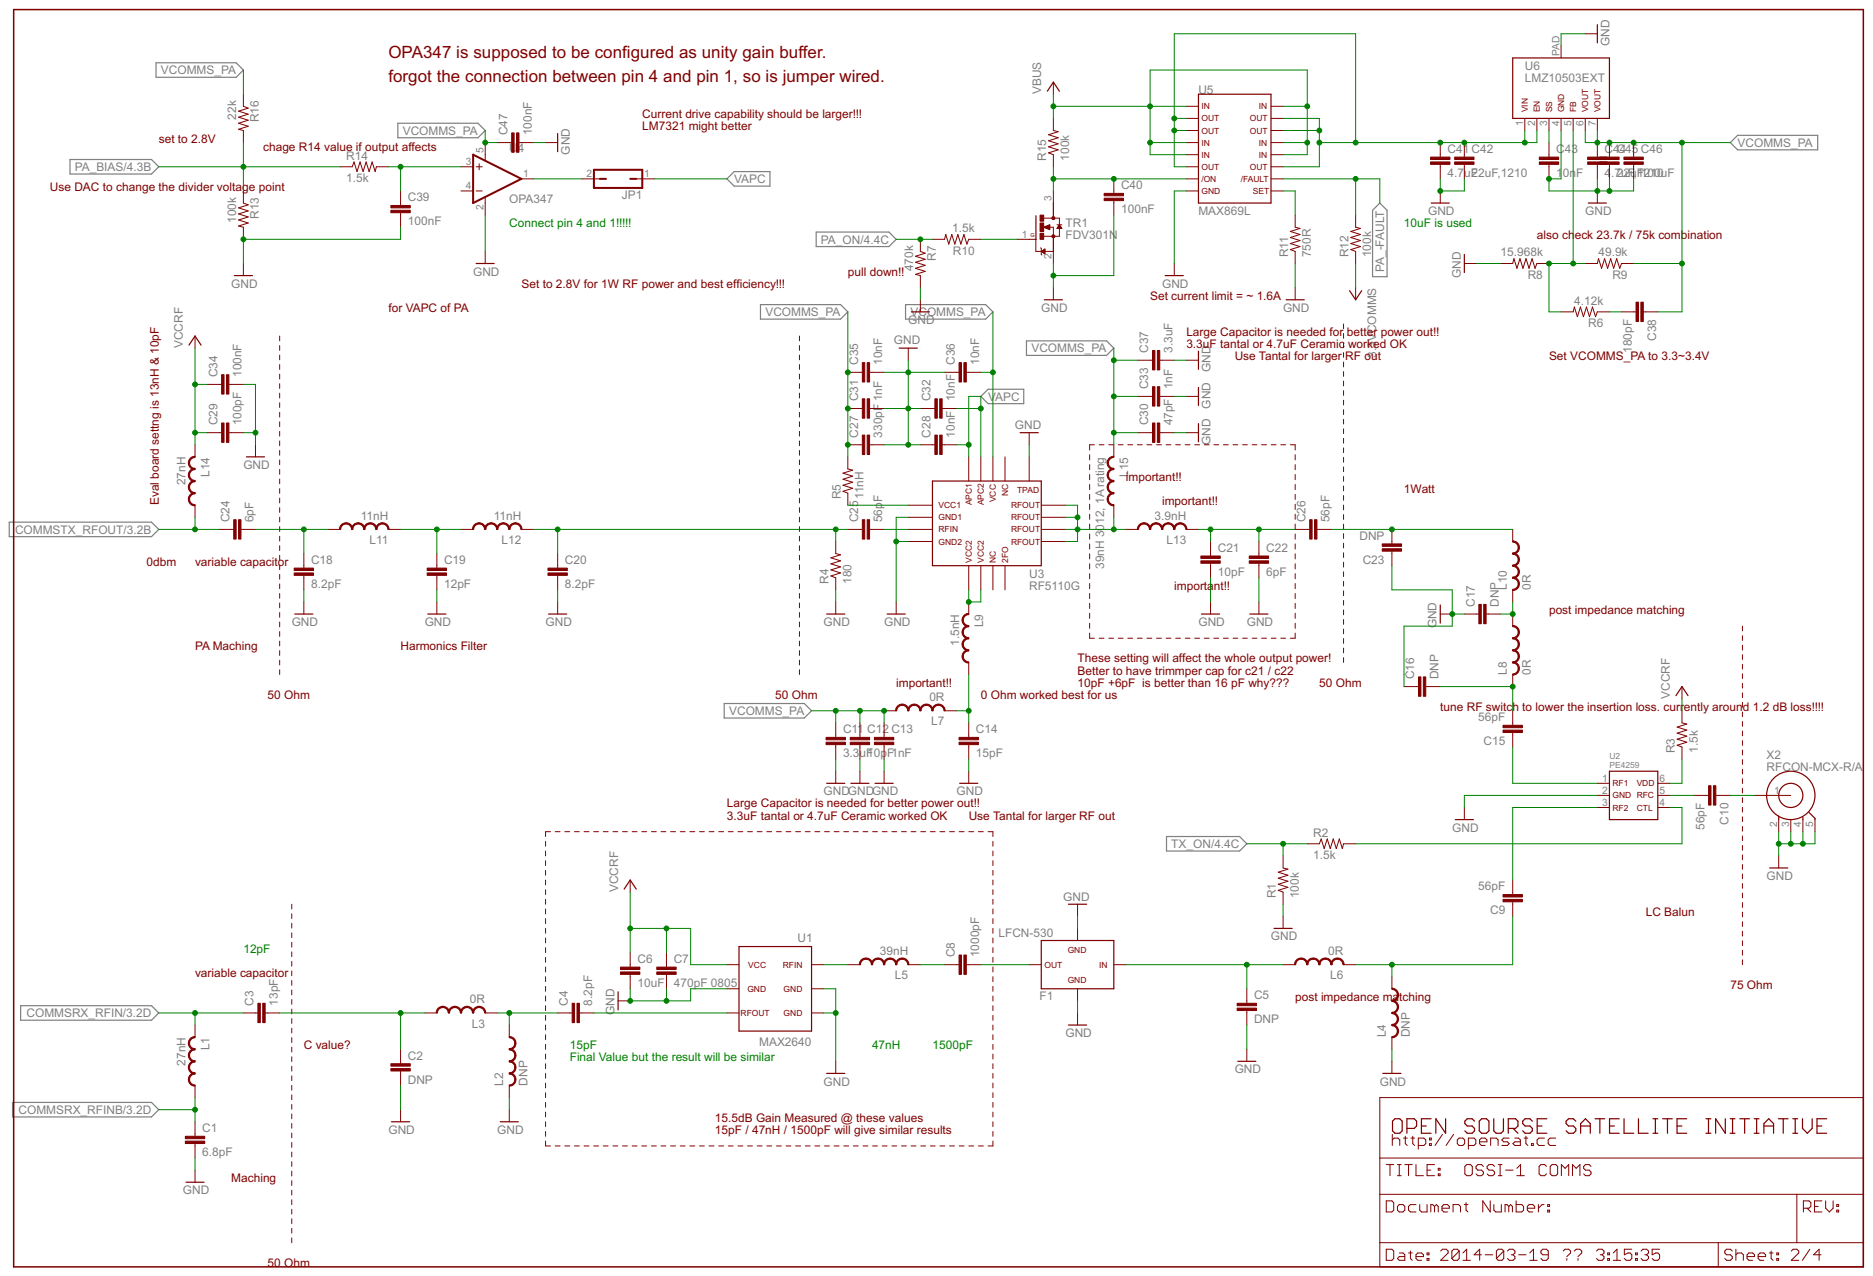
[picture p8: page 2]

OPA347 is supposed to be configured as unity gain buffer.
forgot the connection between pin 4 and pin 1, so is jumper wired. LM7321 might better

Current drive capability should be larger!!!

chage R14 value if output affects

PA_BIAS/4.3B
Use DAC to change the divider voltage point

Set to 2.8V for 1W RF power and best efficiency!!!

for VAPC of PA

Eval board settng is 13nH & 10pF

47pF 1nF 3.3uF GND GND GND
Large Capacitor is needed for better power out!!
3.3uF tantal or 4.7uF Ceramic worked OK

Use Tantal for larger RF out

2FO RFOUT RFOUT RFOUT RFOUT NC

These setting will affect the whole output power!
Better to have trimmper cap for c21 / c22
10pF +6pF is better than 16 pF why???

0 Ohm worked best for us

tune RF switch to lower the insertion loss. currently around 1.2 dB loss!!!!

Final Value but the result will be similar

15.5dB Gain Measured @ these values 15pF / 47nH / 1500pF will give similar results

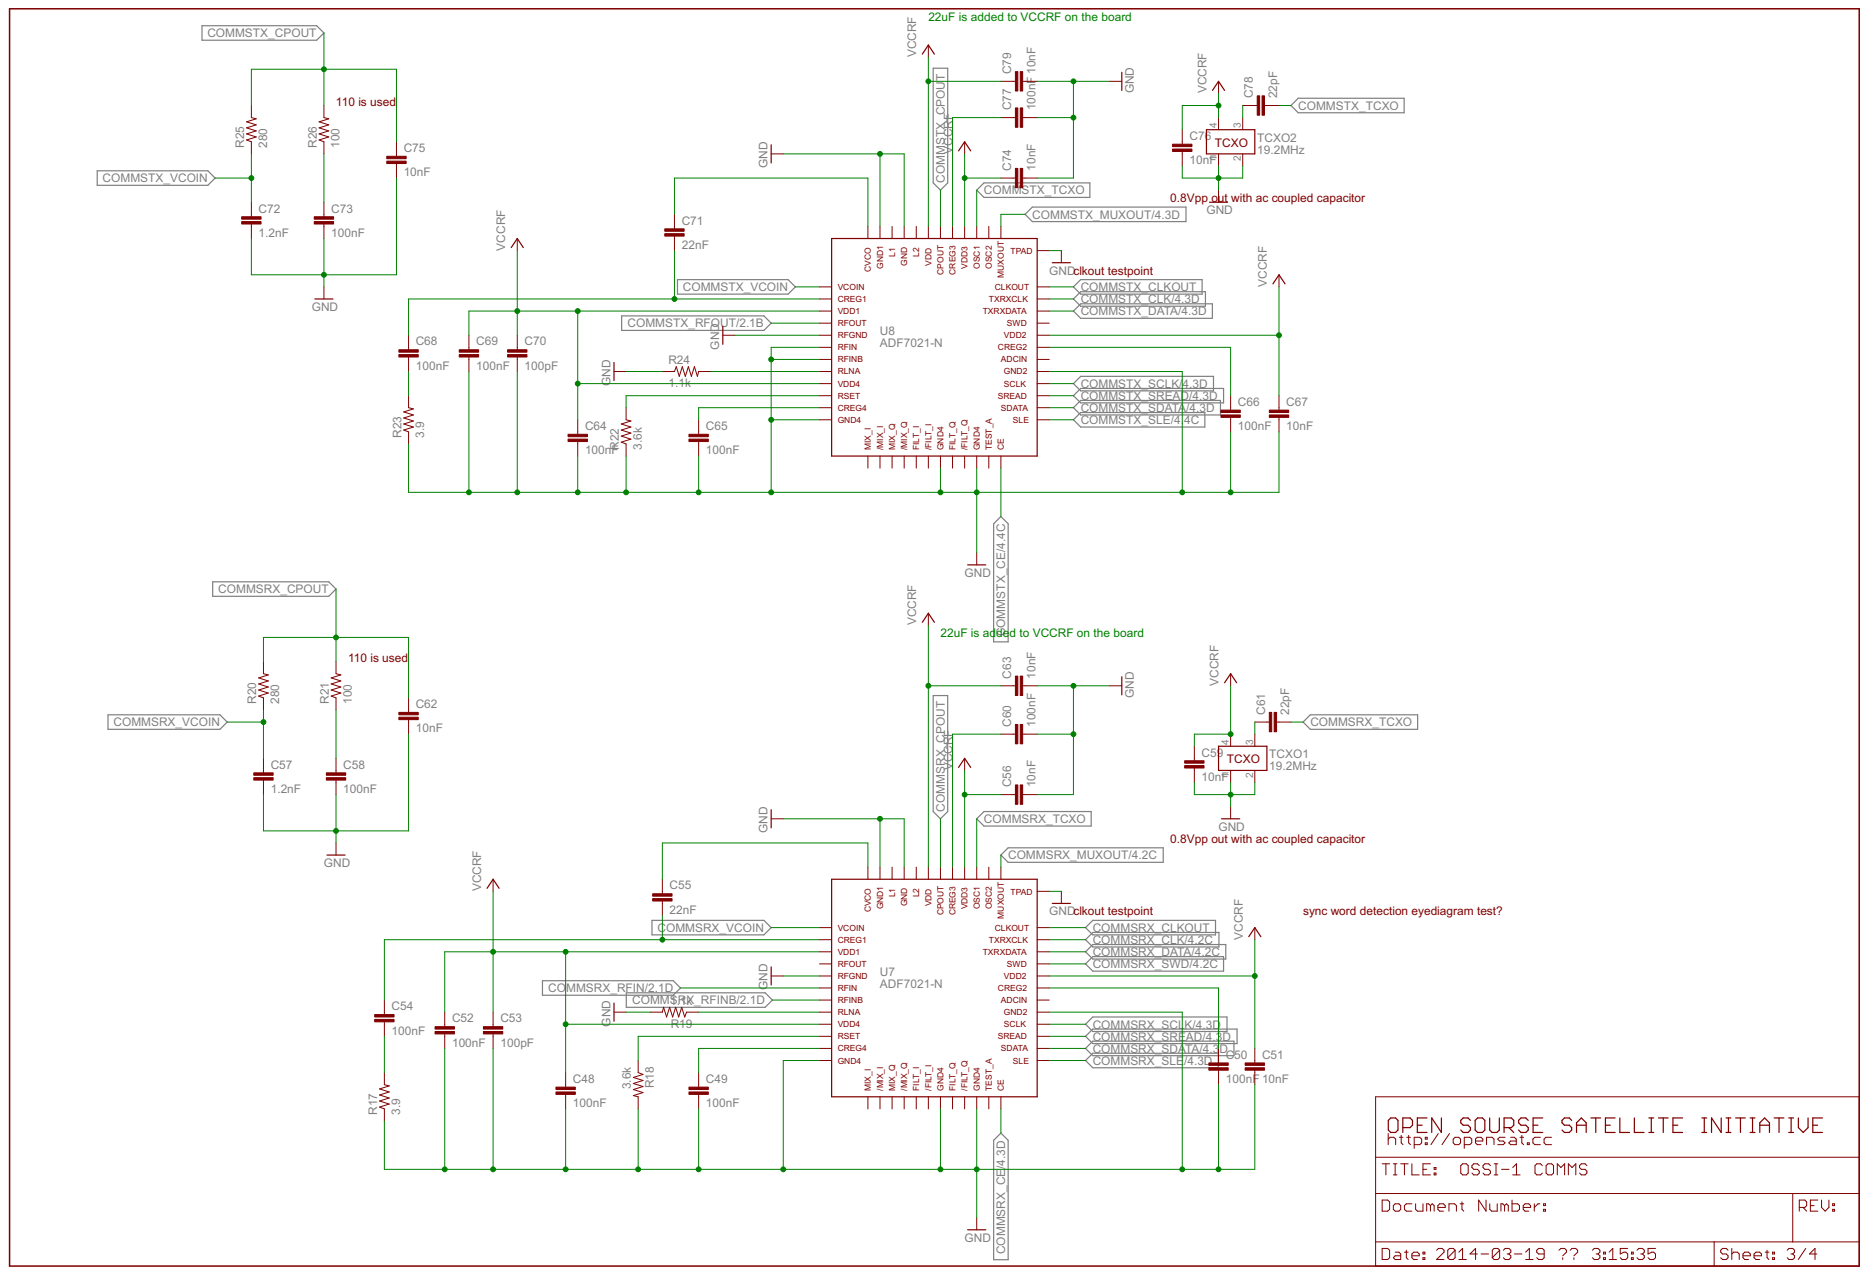
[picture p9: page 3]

22uF is added to VCCRF on the board

0.8Vpp out with ac coupled capacitor

TXRXCLK CLKOUT MUXOUT OSC2 OSC1 VDD3 CREG3 CPOUT VD

sync word detection eyediagram test?

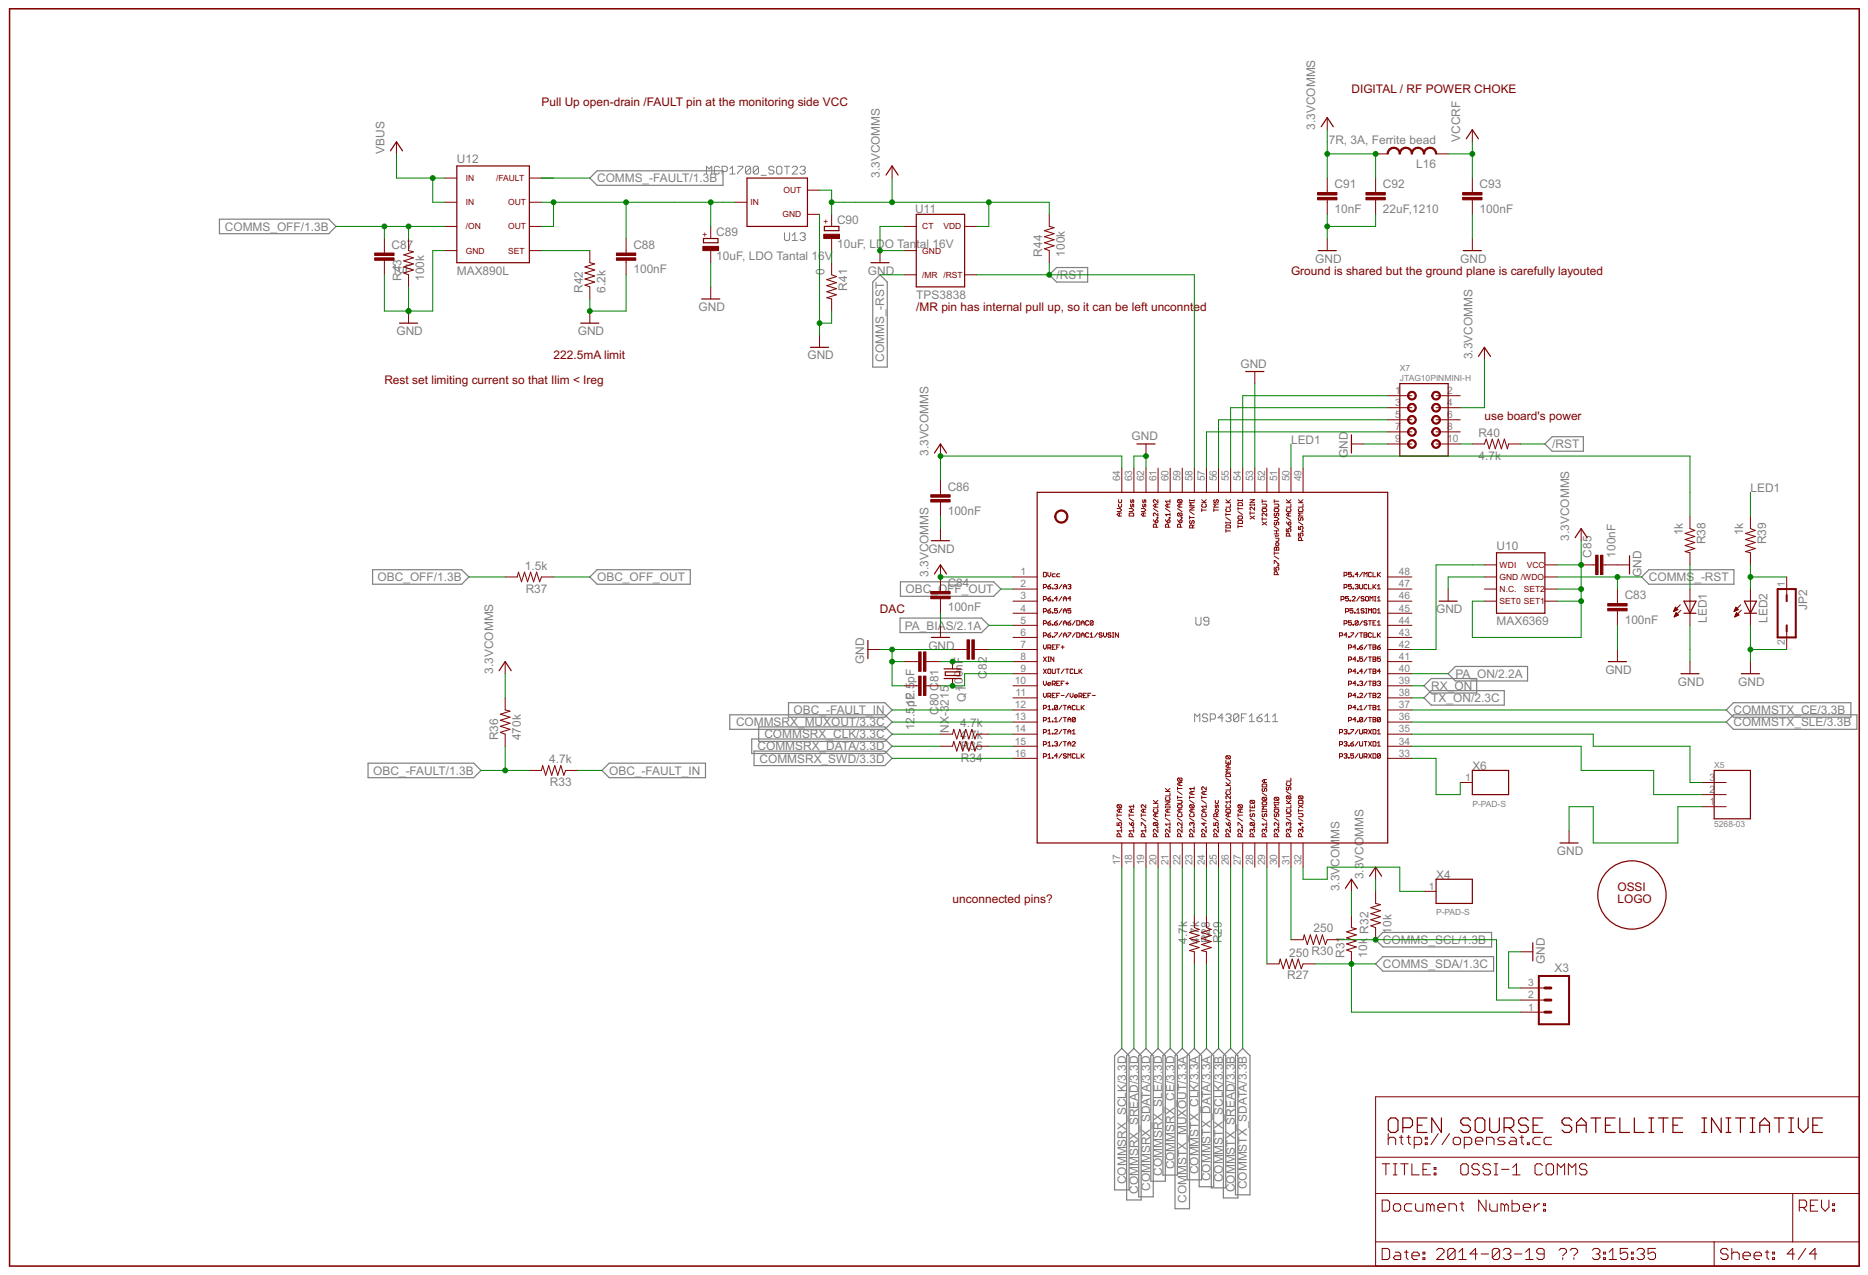
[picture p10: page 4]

DIGITAL / RF POWER CHOKE

Pull Up open-drain /FAULT pin at the monitoring side VCC

Ground is shared but the ground plane is carefully layouted

/RST
TPS3838
/MR pin has internal pull up, so it can be left unconnted

Rest set limiting current so that Ilim < Ireg

LED1

8 | | 41
9 | | 40

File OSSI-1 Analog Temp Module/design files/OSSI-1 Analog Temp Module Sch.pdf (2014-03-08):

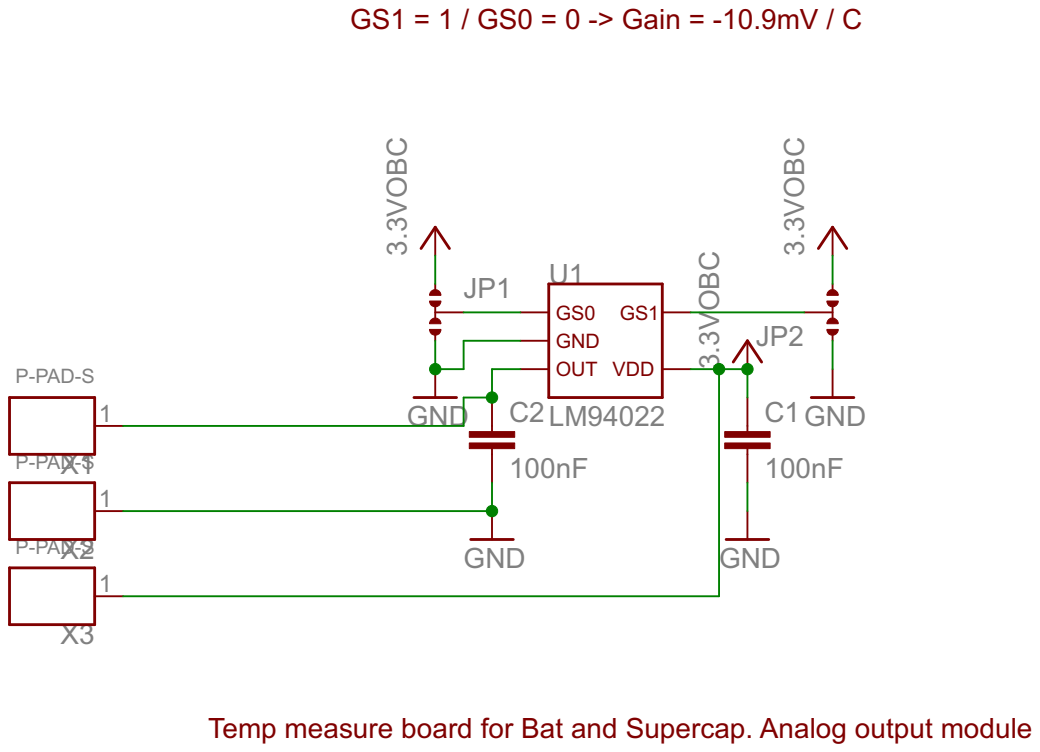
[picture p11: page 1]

Temp measure board for Bat and Supercap. Analog output module

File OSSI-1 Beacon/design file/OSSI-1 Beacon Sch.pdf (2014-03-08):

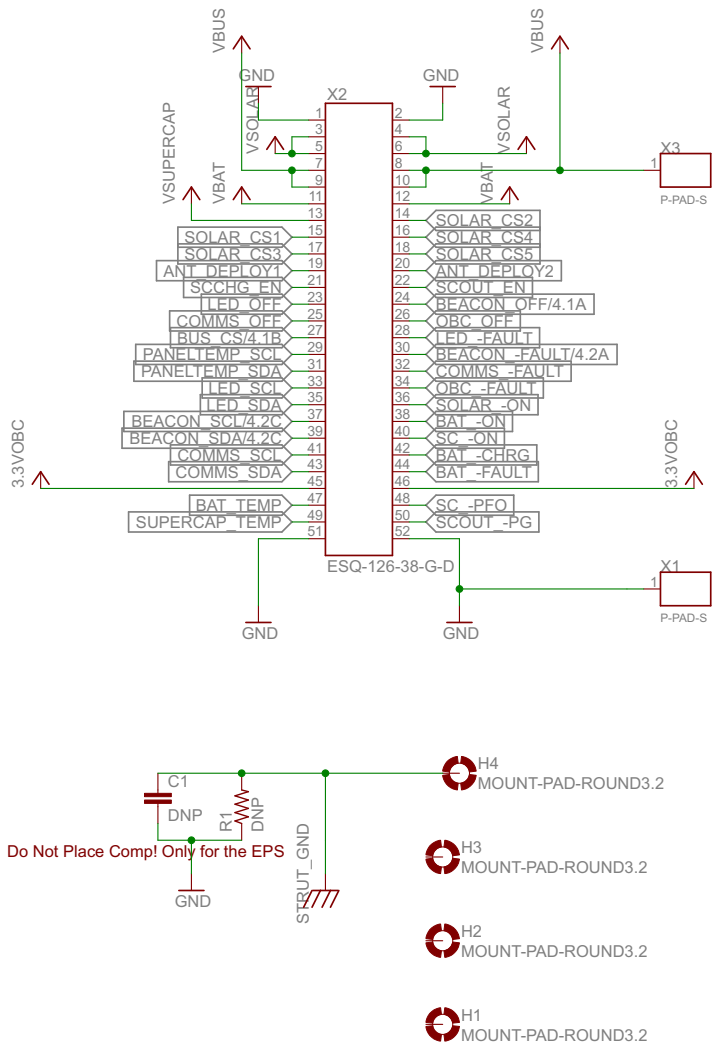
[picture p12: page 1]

Do Not Place Comp! Only for the EPS

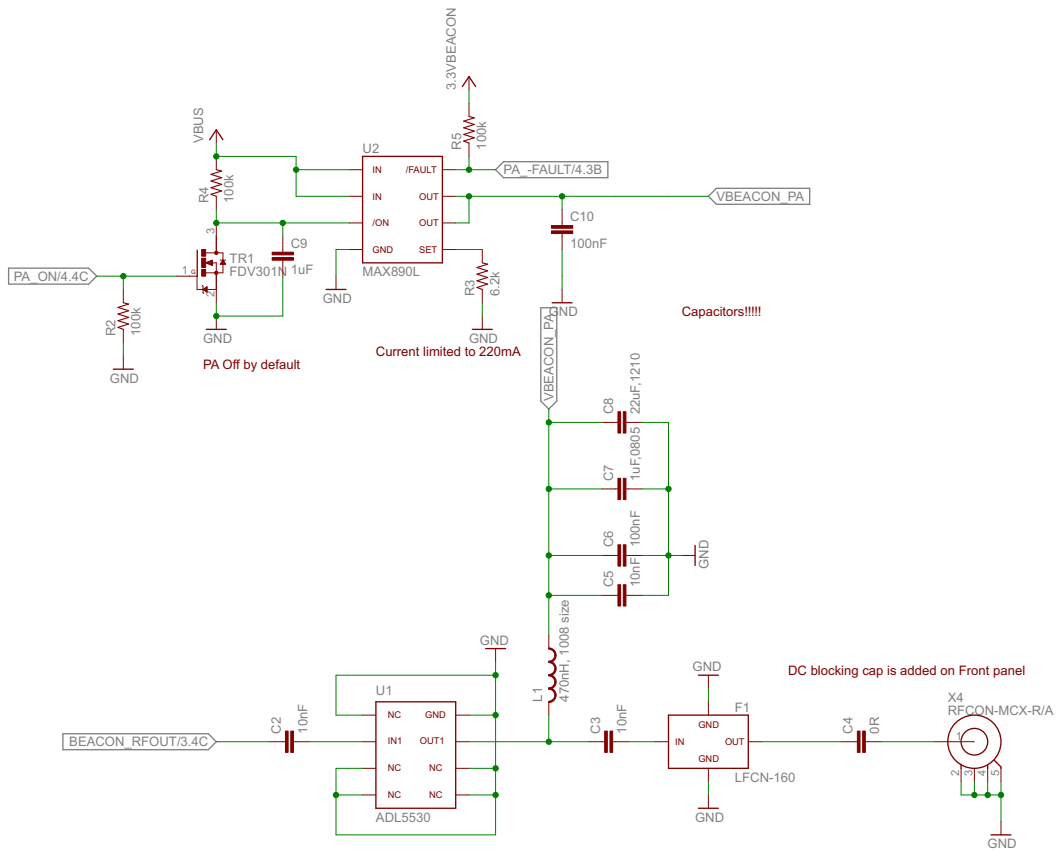
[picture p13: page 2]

PA Off by default

DC blocking cap is added on Front panel NC
GND OUT1 NC

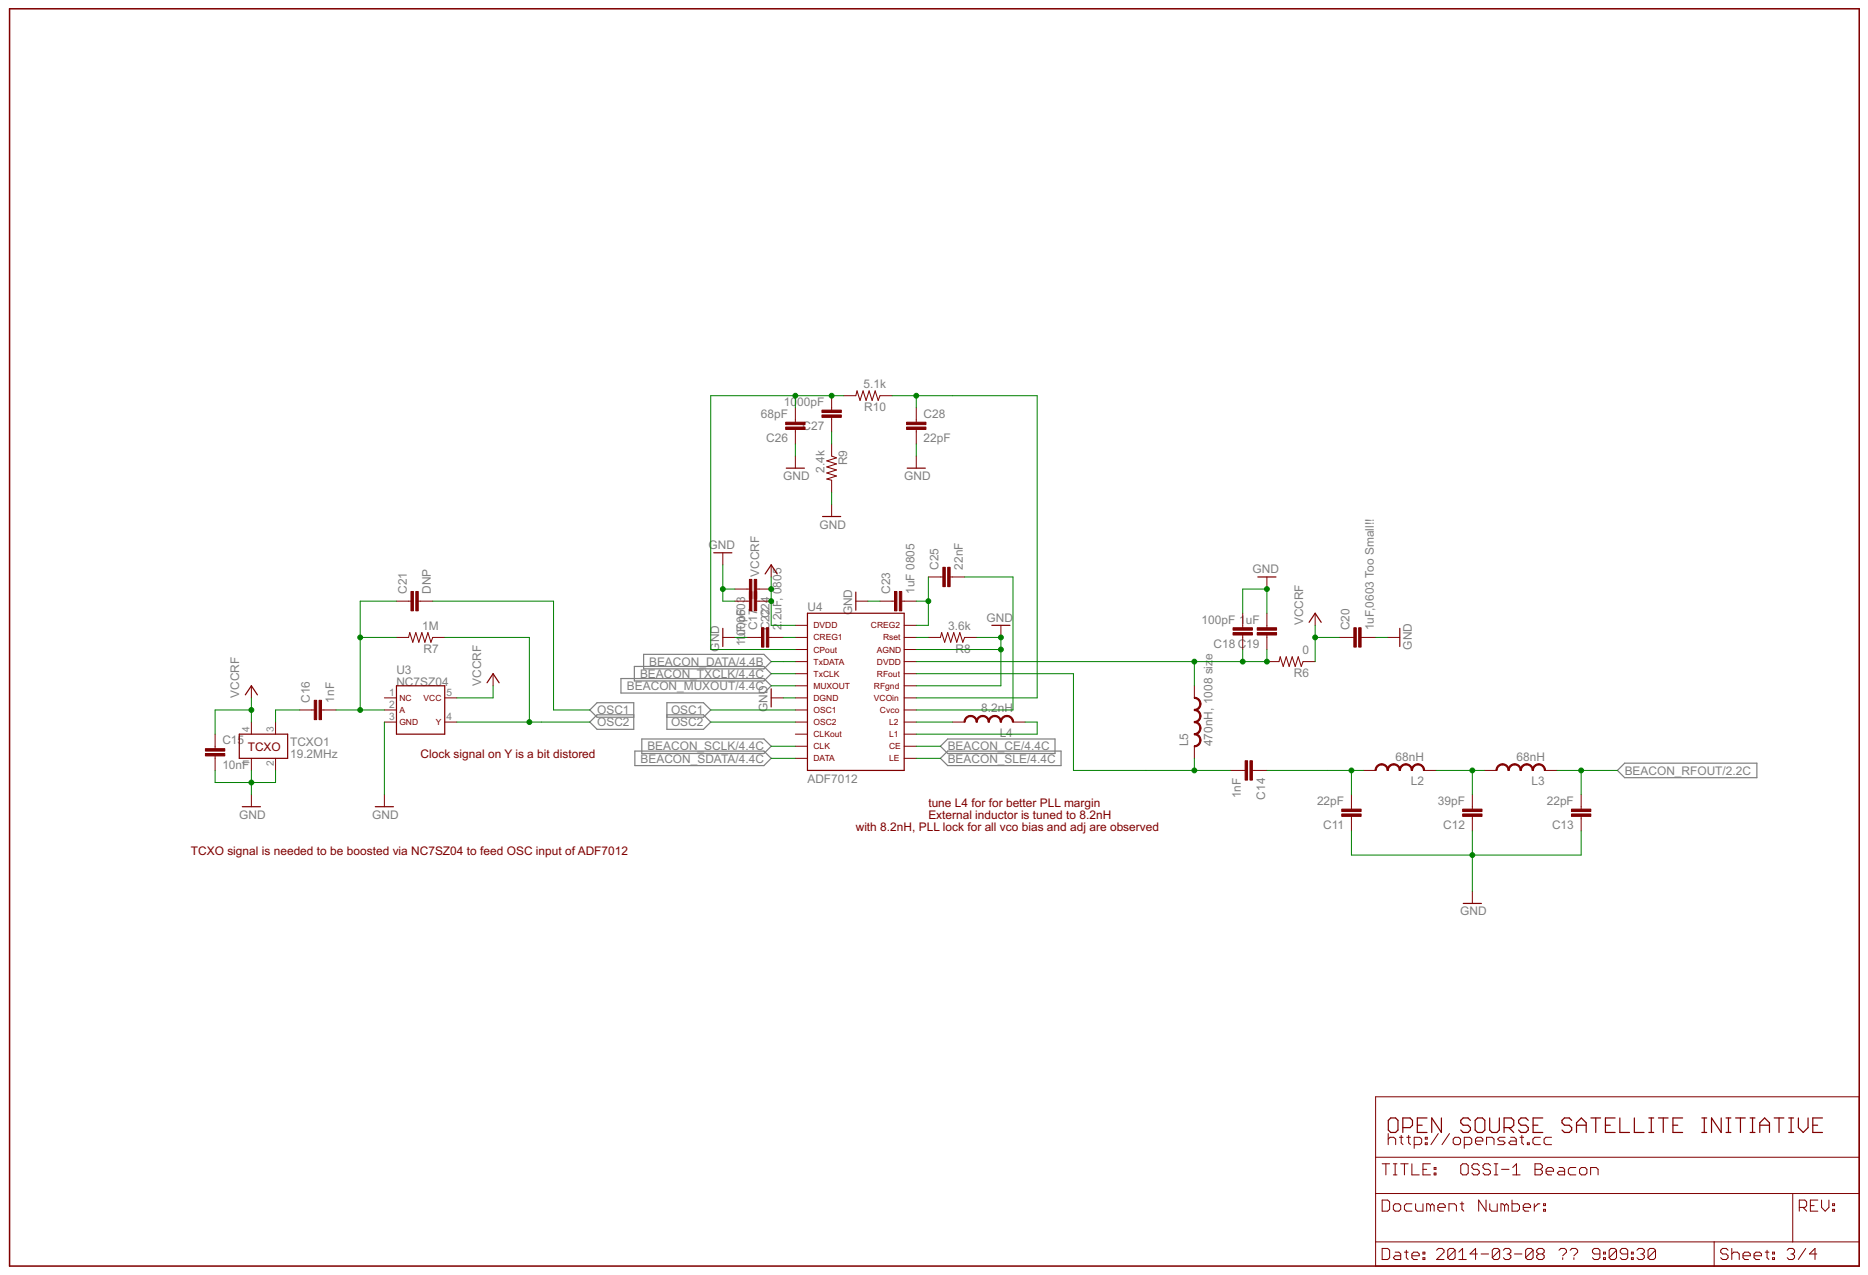
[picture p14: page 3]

2.2uF, 0805 GND
CREG1 CPout TxDATA MUXOUT DGND OSC1 OSC2 CLKout CLK DATA
L2 Cvco VCOin RFgnd RFout DVDD

tune L4 for for better PLL margin Clock signal on Y is a bit distored

External inductor is tuned to 8.2nH

with 8.2nH, PLL lock for all vco bias and adj are observed

TCXO signal is needed to be boosted via NC7SZ04 to feed OSC input of ADF7012

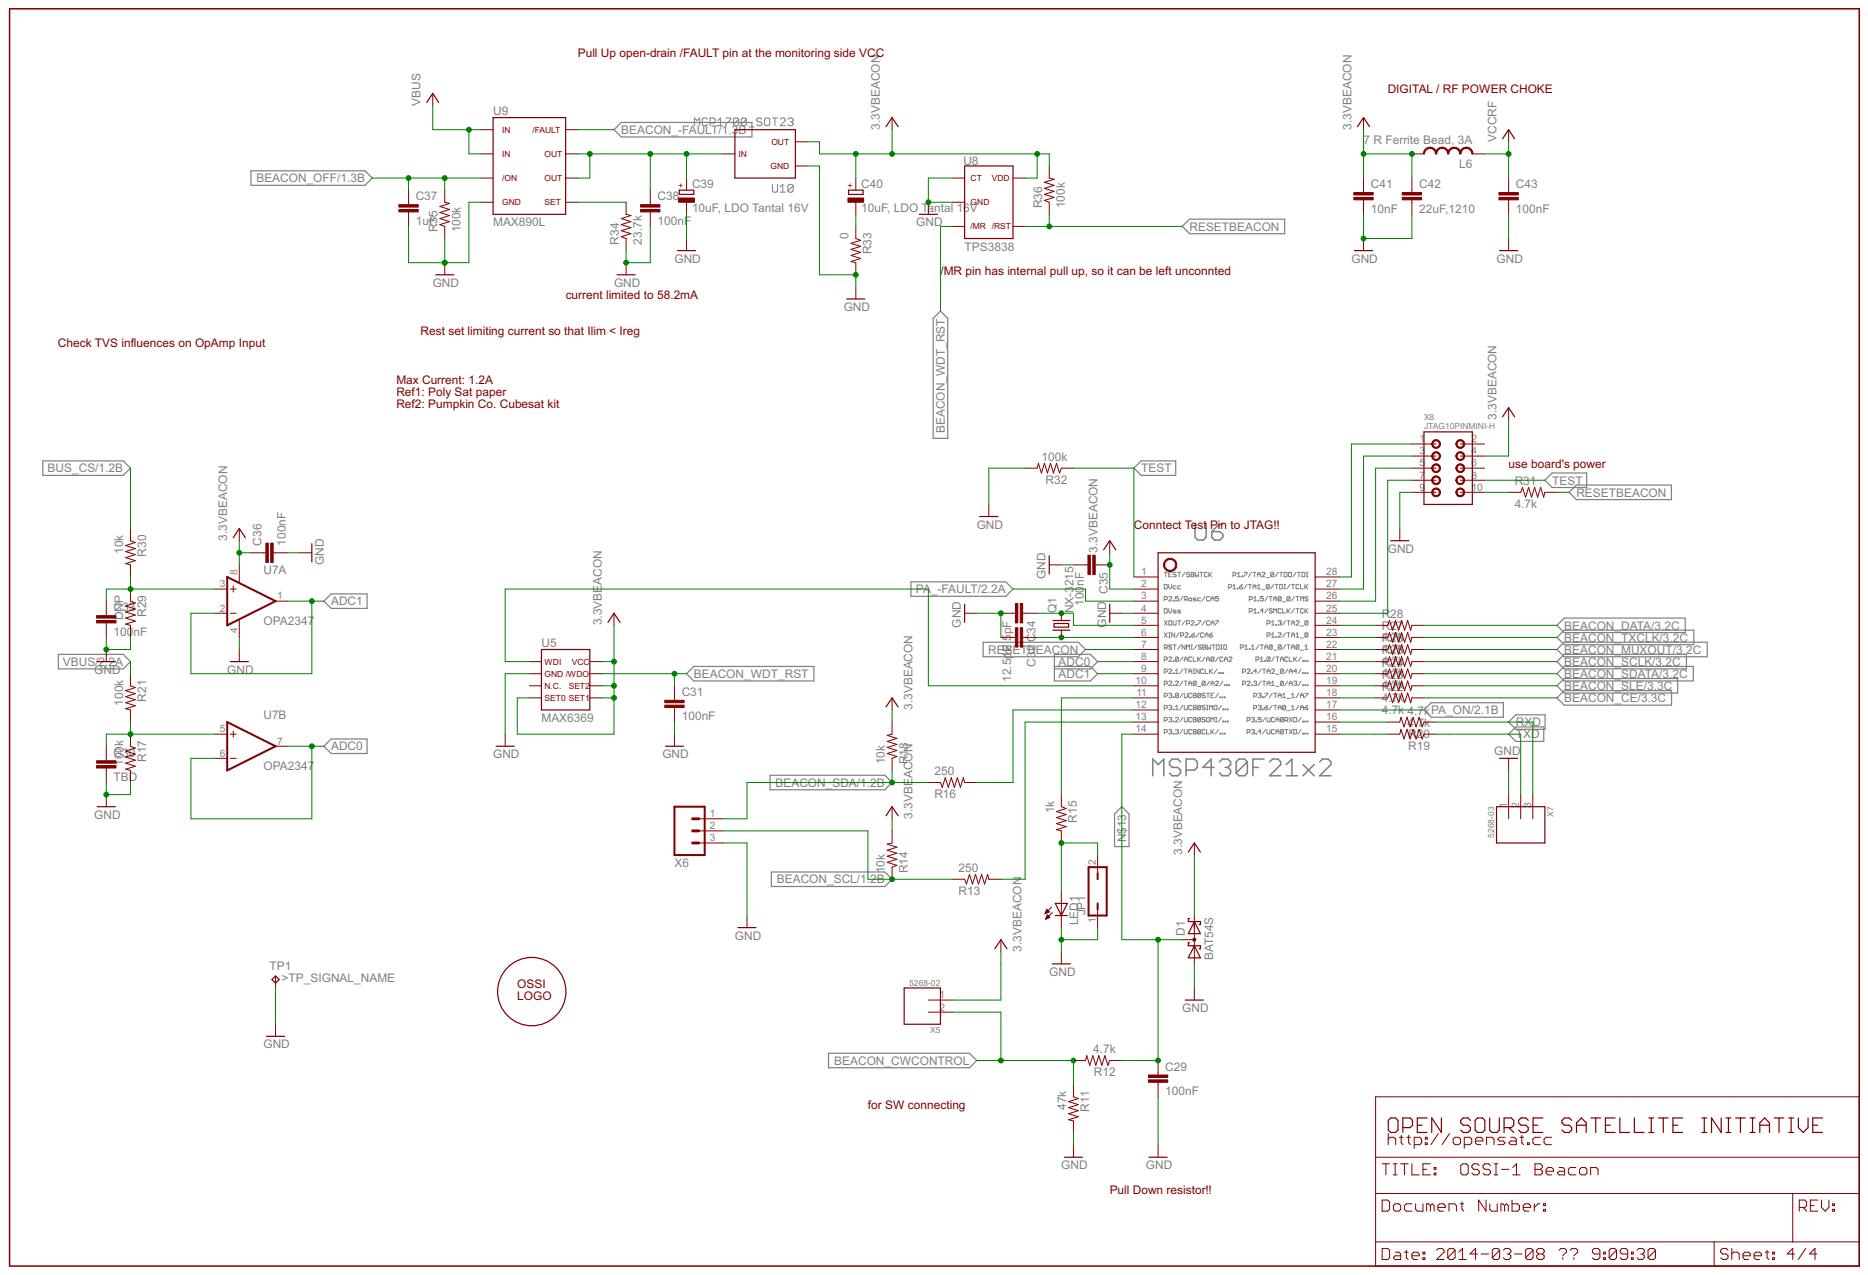
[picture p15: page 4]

Pull Up open-drain /FAULT pin at the monitoring side VCC

DIGITAL / RF POWER CHOKE

/MR pin has internal pull up, so it can be left unconnted

Rest set limiting current so that Ilim < Ireg

Check TVS influences on OpAmp Input

Max Current: 1.2A
Ref1: Poly Sat paper Ref2: Pumpkin Co. Cubesat kit

9 | 10

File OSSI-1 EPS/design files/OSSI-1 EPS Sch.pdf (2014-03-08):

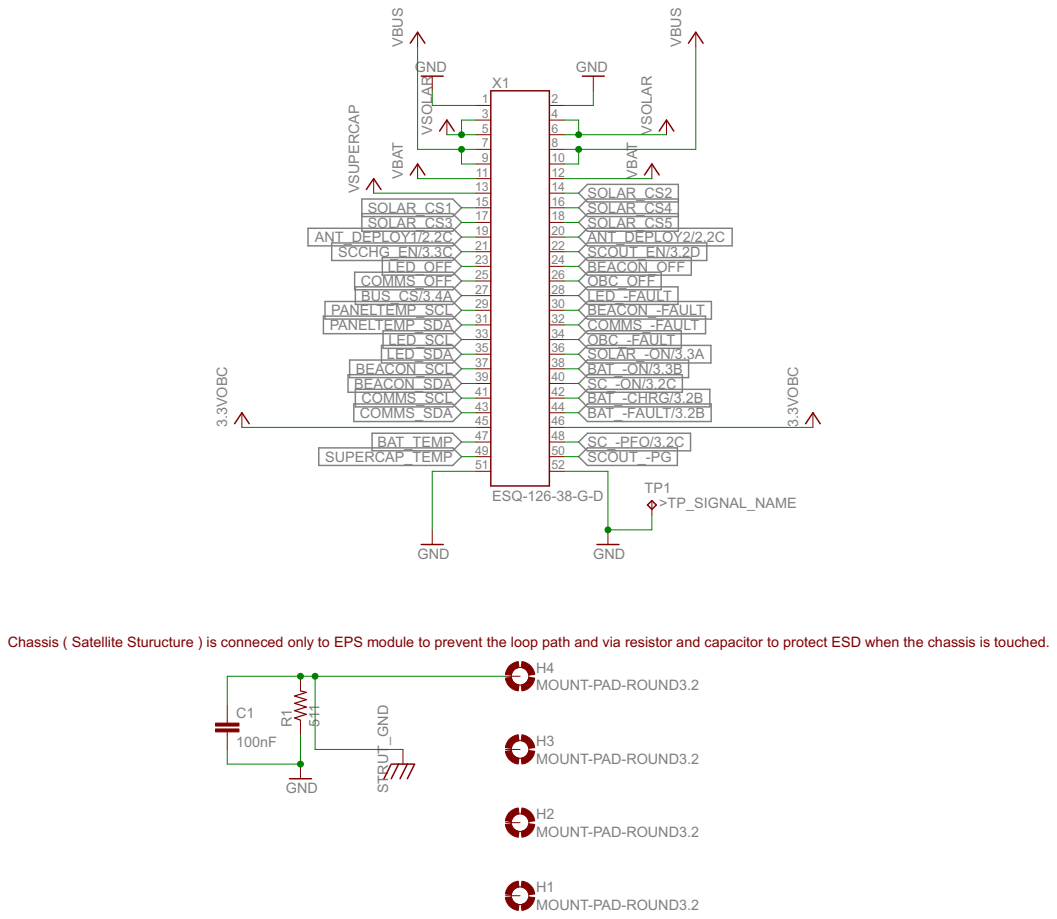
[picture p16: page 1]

Chassis ( Satellite Sturucture ) is conneced only to EPS module to prevent the loop path and via resistor and capacitor to protect ESD when the chassis is touched.

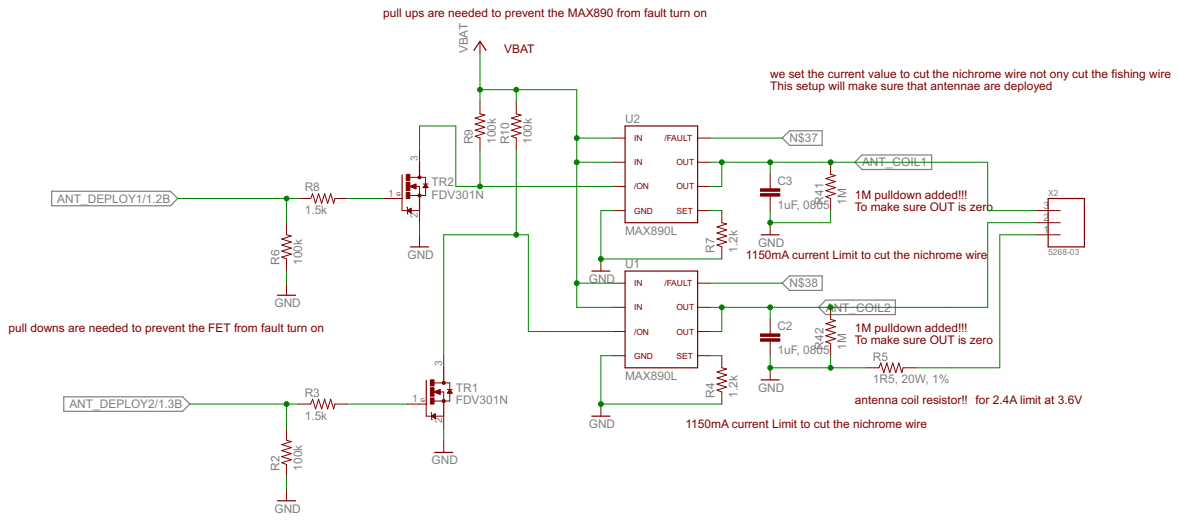
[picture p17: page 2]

1M pulldown added!!!
To make sure OUT is zero

GND
1150mA current Limit to cut the nichrome wire

ANT_COIL2

pull downs are needed to prevent the FET from fault turn on

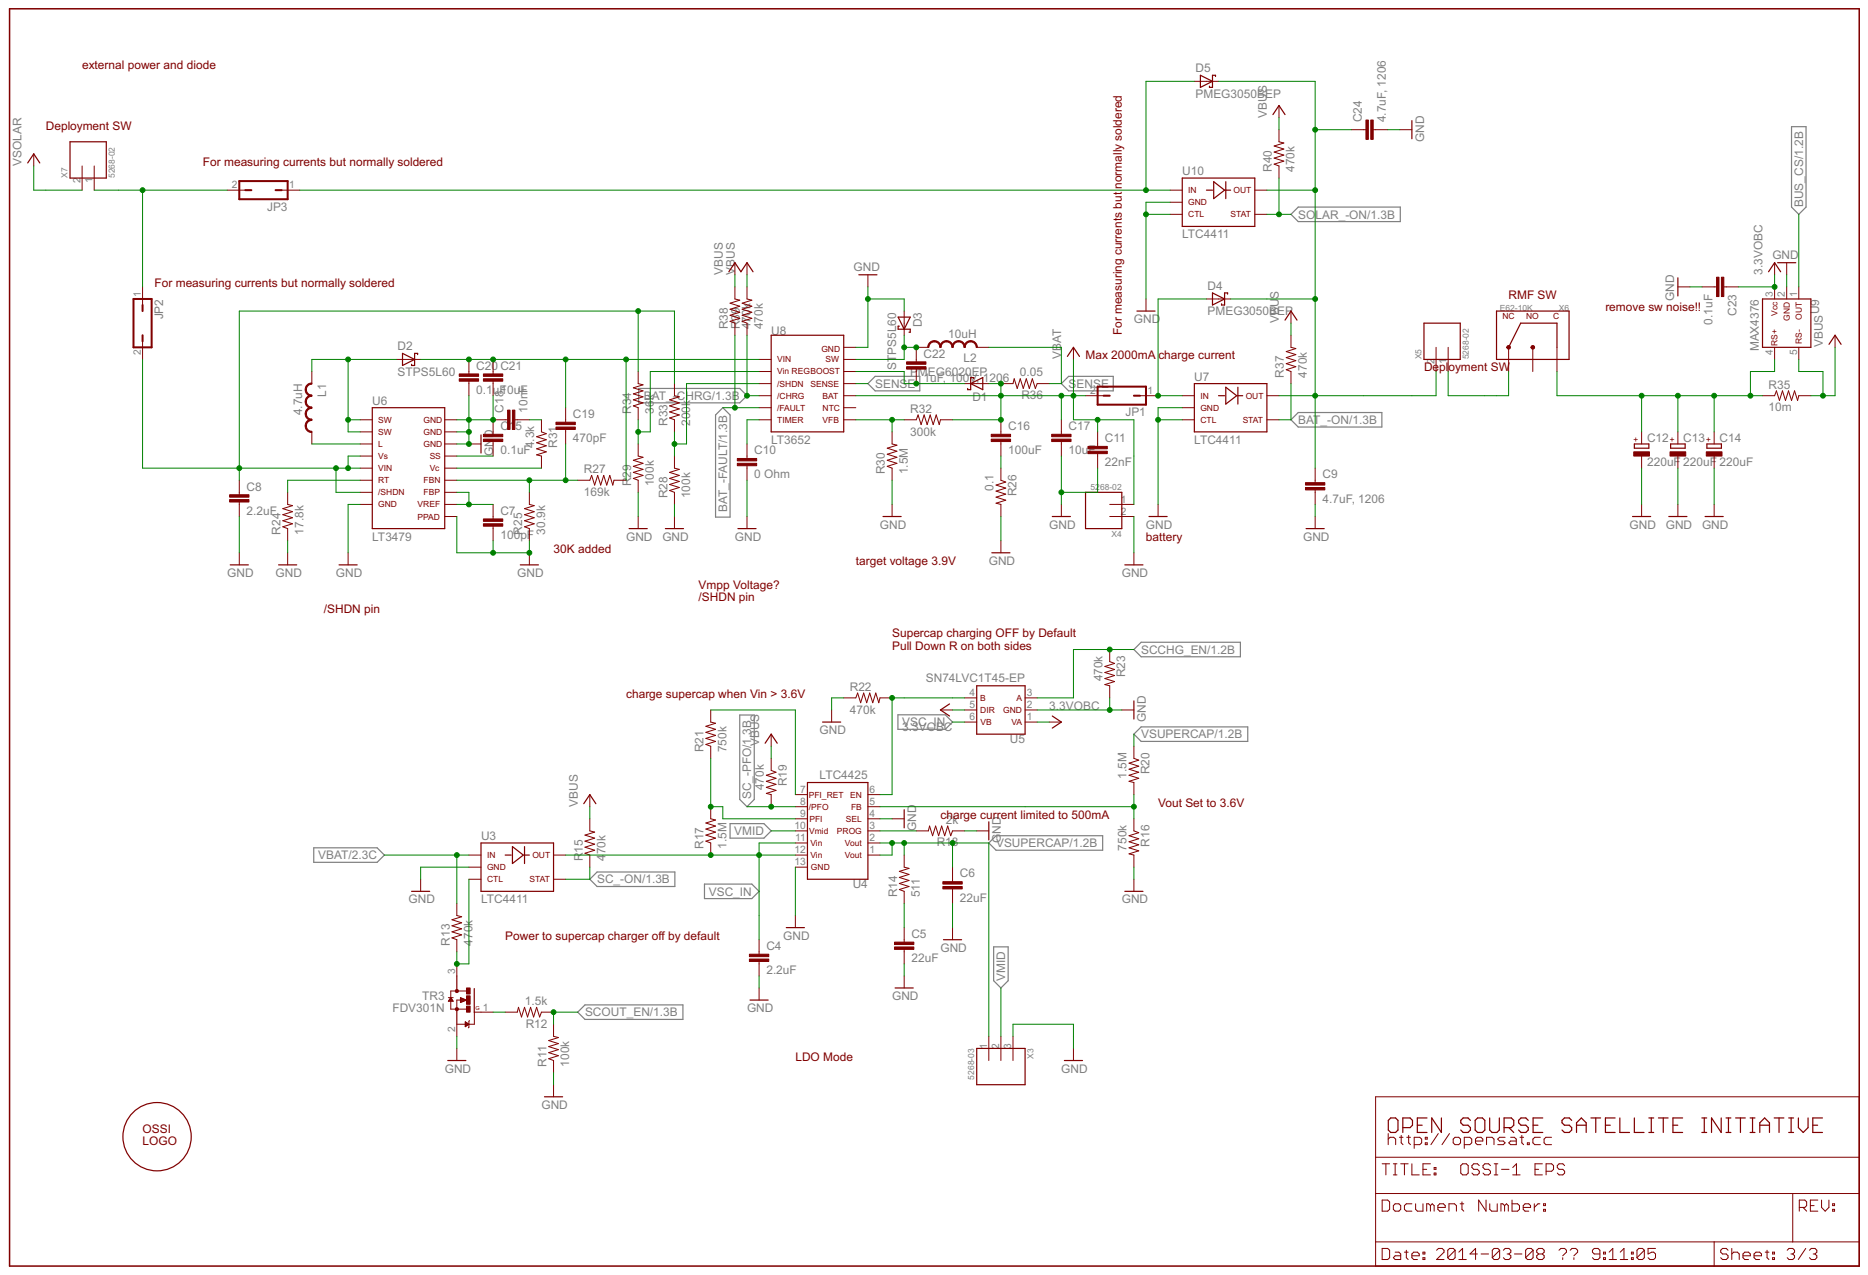
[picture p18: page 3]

external power and diode Deployment SW

For measuring currents but normally soldered

/SHDN pin Vmpp Voltage?

Supercap charging OFF by Default
Pull Down R on both sides

charge supercap when Vin > 3.6V

charge current limited to 500mA

Power to supercap charger off by default

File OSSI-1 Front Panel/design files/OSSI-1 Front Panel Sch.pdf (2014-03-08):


GND
Connect 12pF ceramic Cap from the L3 to GND
12pF cap connected to 1 turn from X6 and Ground

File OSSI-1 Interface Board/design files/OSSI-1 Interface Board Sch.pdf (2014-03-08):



test point?? nattery voltage??

Do Not Place Comp! Only for the EPS

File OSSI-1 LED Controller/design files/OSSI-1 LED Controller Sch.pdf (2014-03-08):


Disconnect VSUPERCAP here as EPS provides measurement signal to OBC

Do Not Place Comp! Only for the EPS


Max VSupercap lmited to 3.6V by EPS

Pull Up open-drain /FAULT pin at the monitoring side VCC

3.3VLED
Power supplied from 3.3VLED to be more predictable

Cp out = 7.2V when Vsupercap = 3.6V

/MR pin has internal pull up, so it can be left unconnted

GND
Rest set limiting current so that Ilim < Ireg

Input protection needed when PWM ON, VSUPERCAP OFF

op-amp is configured as a comparator

Non-Inverting Amp, Gain ~ = 3

4 | 25
5 | 22 21 20 19

set Current to 10A
10A - > 2.5V out from current sensor @ 0.005 R sense, @ G = 50

These resistor values has to be tuned by measuring the currents

Chagnge these 3 Resistor value to set the limit current!!!!!
Currently set to 9.7A

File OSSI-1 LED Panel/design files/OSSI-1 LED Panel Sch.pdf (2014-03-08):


LED-P7 LED-P7 LED-P7 LED-P7 P-PAD P-PAD LED1 LED2 LED3 LED4 1X1 1 X2 LED+ LED-

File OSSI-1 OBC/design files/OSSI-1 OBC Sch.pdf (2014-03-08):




interface side select power from Solar or 5V adaptor

This section needs pullup resistor as the other sides are pulled up!!! same conditon for both sides!

120, DNP GND
VEXT On by default to charge the battery from VEXT

All pull up to VBUS

But can be turned off by OBC for testing

VEXT will turn on the 485 in Receiver mode

DE pin to OBC

OBC pull high DE pin when TX

Short warning! modify layout!!!

DVss AVdd MOSI SCLK

2 | | 15
3 | | 14

critical signal should be directly connect to MCU


Pull Up open-drain /FAULT pin at the monitoring side VCC

EN is Active High
Vout Overshoot check

Remove 0 Ohm for SMCLK / ACLK out

Rest set limiting current so that Ilim < Ireg

/MR pin has internal pull up, so it can be left unconnted

Max Current: 1.2A
Ref1: Poly Sat paper Ref2: Pumpkin Co. Cubesat kit

ROSC for better DCO

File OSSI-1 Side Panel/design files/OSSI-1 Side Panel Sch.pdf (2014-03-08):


MOUNT-PAD-ROUNMD2O.U1NT-PAD-ROUND2M.1OUNT-PAD-ROUND2M.1OUNT-PAD-ROUND2.1 STRUT_GND

pull-up resistor needed?

power supplied by OBC



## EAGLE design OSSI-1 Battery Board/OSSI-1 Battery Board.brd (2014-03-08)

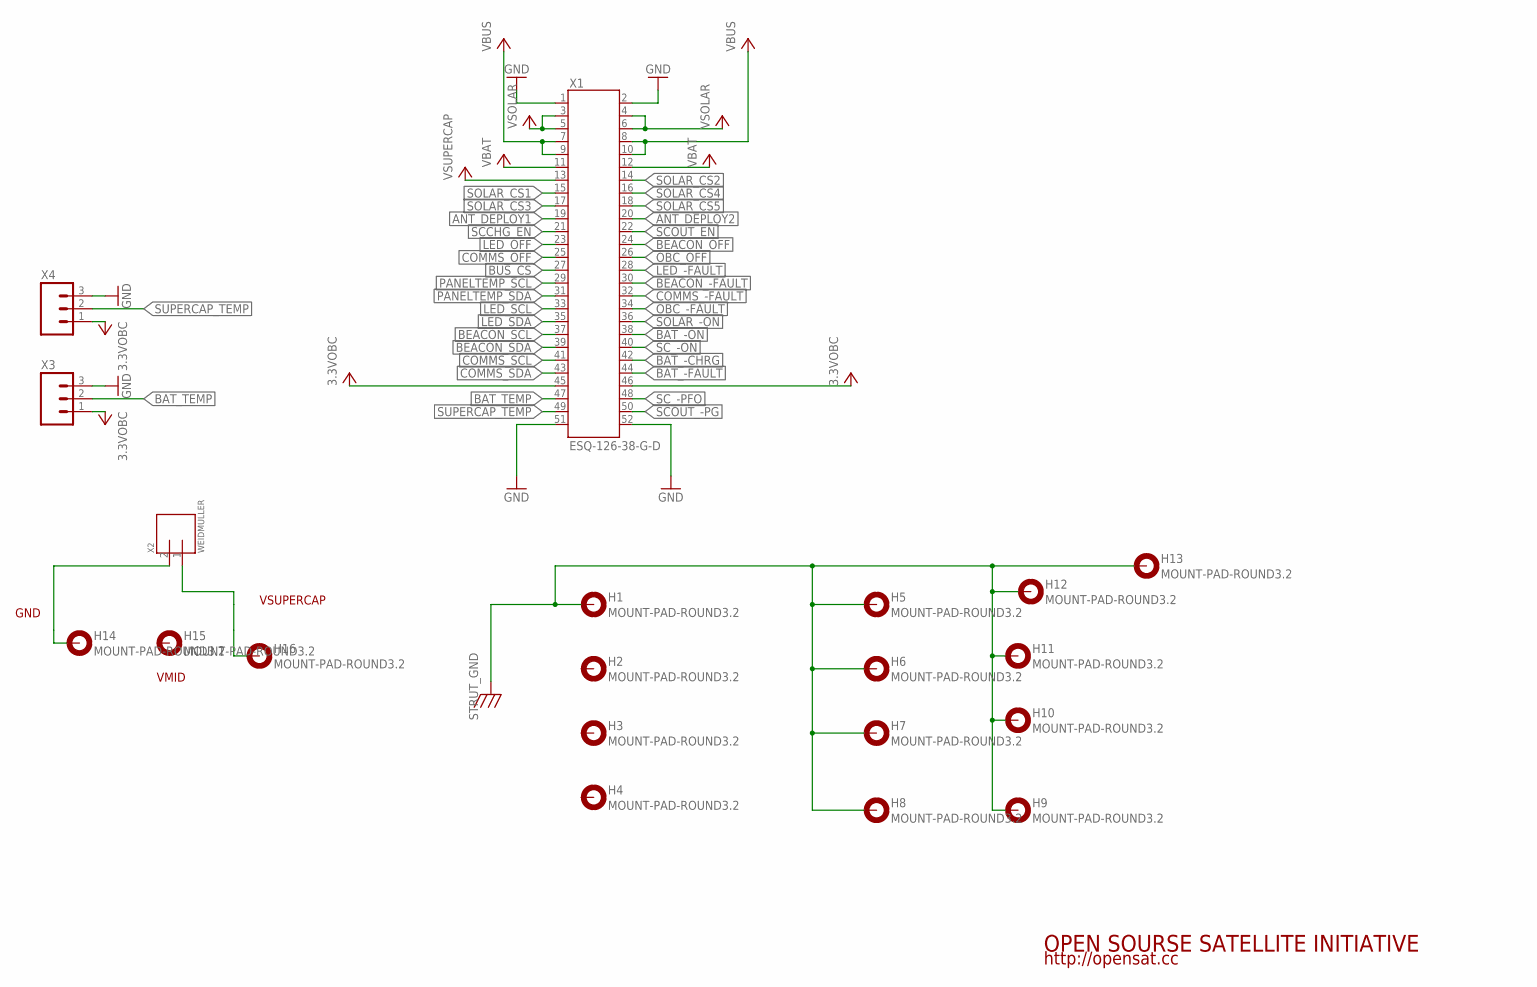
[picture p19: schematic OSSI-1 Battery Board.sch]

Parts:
H1, H2, H3, H4, H5, H6, H7, H8, H9, H10, H11, H12, H13, H14, H15, H16: MOUNT-PAD-ROUND3.2; 3.2-PAD-ROUND
X1: ESQ-126-38-G-D; ESQ-126-XX-X-D
X2: WEIDMULLER; WEIDMULLER1760490000
X3, X4: M03PTH; 1X03

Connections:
3.3VOBC: X1.45, X1.46, X3.1, X4.1
ANT_DEPLOY1: X1.19
ANT_DEPLOY2: X1.20
BAT_-CHRG: X1.42
BAT_-FAULT: X1.44
BAT_-ON: X1.38
BAT_TEMP: X1.47, X3.2
BEACON_-FAULT: X1.30
BEACON_OFF: X1.24
BEACON_SCL: X1.37
BEACON_SDA: X1.39
BUS_CS: X1.27
COMMS_-FAULT: X1.32
COMMS_OFF: X1.25
COMMS_SCL: X1.41
COMMS_SDA: X1.43
GND: X1.1, X1.2, X1.51, X1.52, X3.3, X4.3
LED_-FAULT: X1.28
LED_OFF: X1.23
LED_SCL: X1.33
LED_SDA: X1.35
unnamed: H14.B3,2, X2.2
unnamed: H16.B3,2, X2.1
OBC_-FAULT: X1.34
OBC_OFF: X1.26
PANELTEMP_SCL: X1.29
PANELTEMP_SDA: X1.31
SCCHG_EN: X1.21
SCOUT_-PG: X1.50
SCOUT_EN: X1.22
SC_-ON: X1.40
SC_-PFO: X1.48
SOLAR_-ON: X1.36
SOLAR_CS1: X1.15
SOLAR_CS2: X1.14
SOLAR_CS3: X1.17
SOLAR_CS4: X1.16
SOLAR_CS5: X1.18
STRUT_GND: H1.B3,2, H5.B3,2, H6.B3,2, H7.B3,2, H8.B3,2, H9.B3,2, H10.B3,2, H11.B3,2, H12.B3,2, H13.B3,2
SUPERCAP_TEMP: X1.49, X4.2
VBAT: X1.11, X1.12
VBUS: X1.7, X1.8, X1.9, X1.10
VSOLAR: X1.3, X1.4, X1.5, X1.6
VSUPERCAP: X1.13

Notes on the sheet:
GND
VSUPERCAP
VMID
OPEN SOURSE SATELLITE INITIATIVE
http://opensat.cc

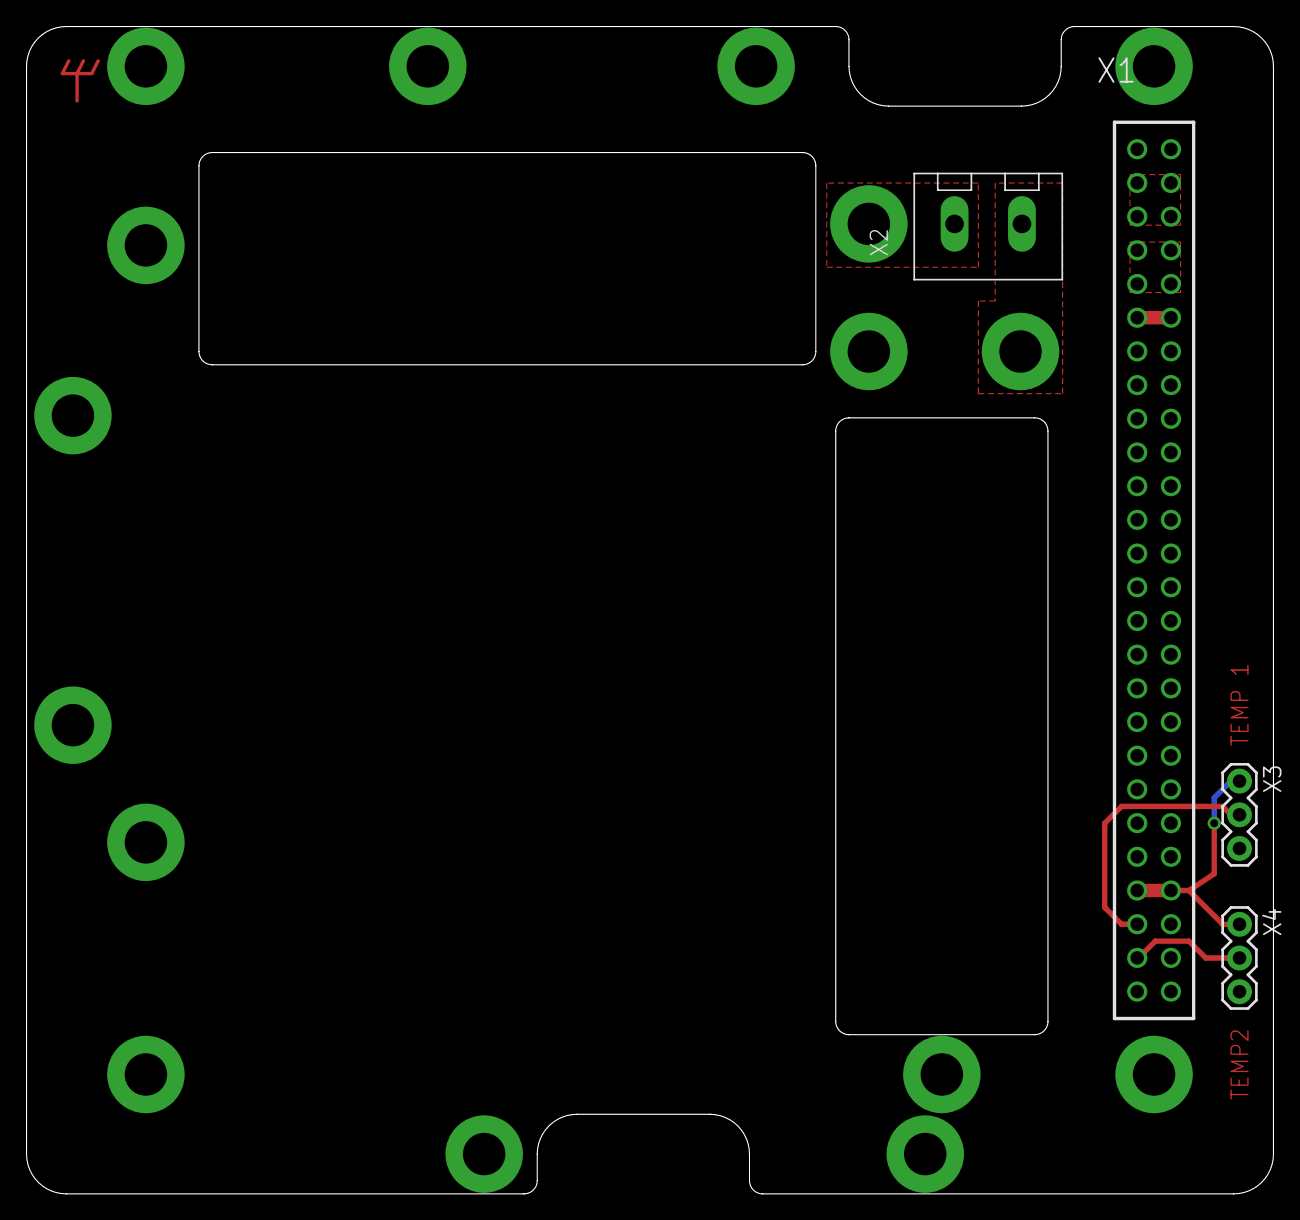
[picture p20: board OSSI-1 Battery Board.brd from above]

Board: 2 copper layers, 94.0 x 88.0 mm, 20 parts (0 on the bottom side), 10 nets.

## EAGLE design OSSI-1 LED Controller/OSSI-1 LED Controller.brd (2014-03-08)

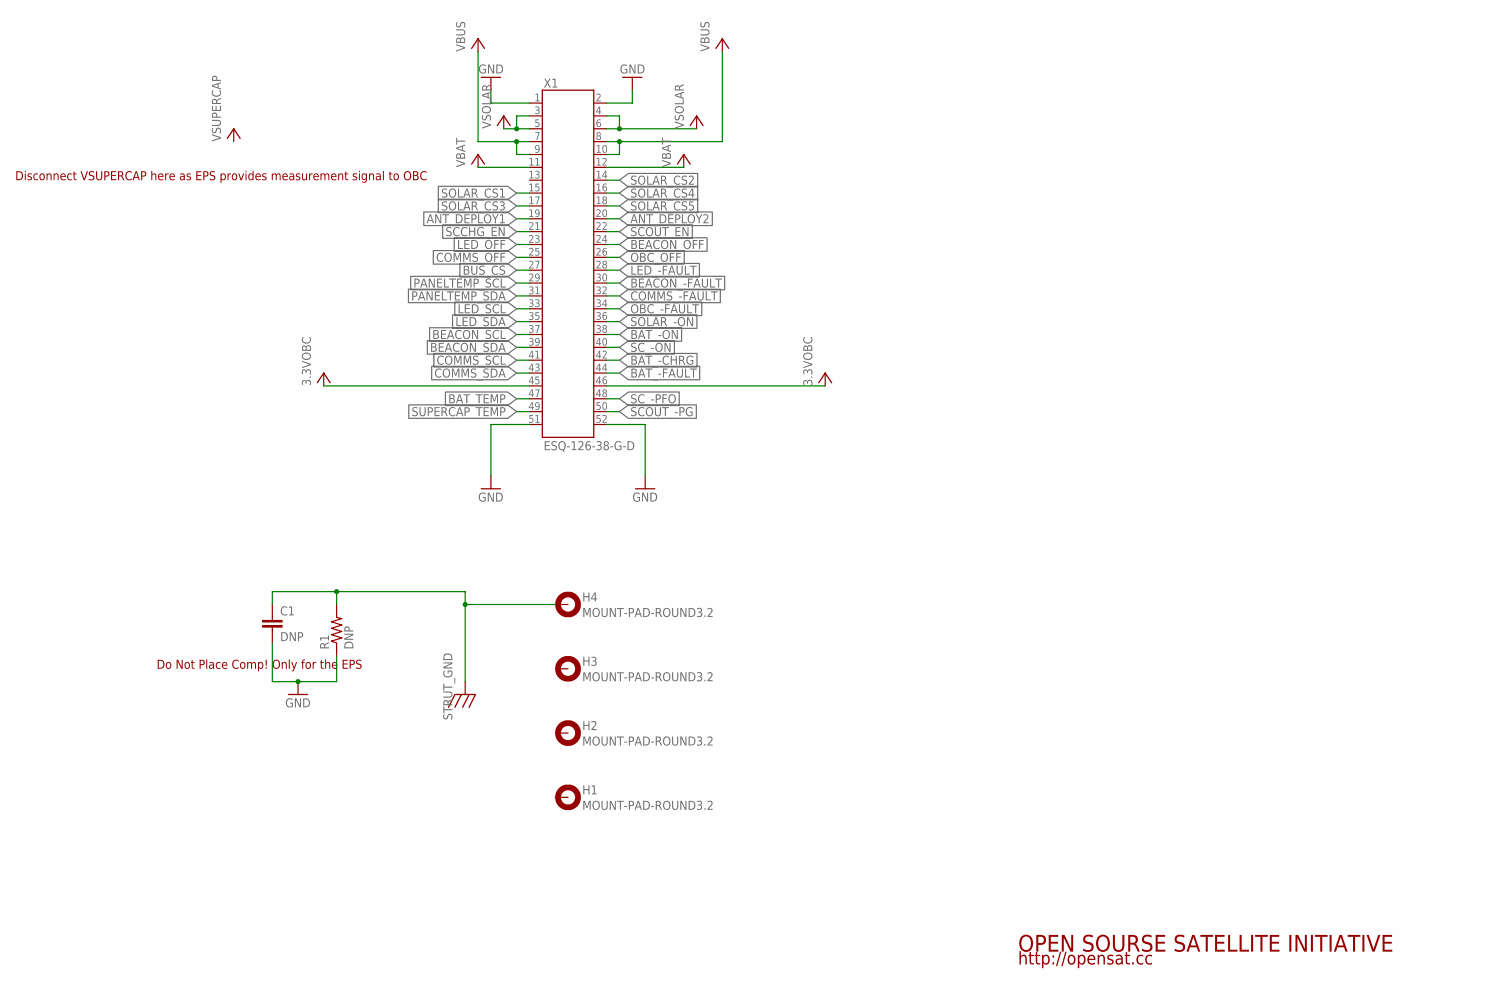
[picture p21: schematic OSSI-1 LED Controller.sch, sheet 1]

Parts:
C1: DNP; C0805(2012)
H1, H2, H3, H4: MOUNT-PAD-ROUND3.2; 3.2-PAD-ROUND
R1: DNP; WSL1206
X1: ESQ-126-38-G-D; ESQ-126-XX-X-D

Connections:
3.3VOBC: X1.45, X1.46
ANT_DEPLOY1: X1.19
ANT_DEPLOY2: X1.20
BAT_-CHRG: X1.42
BAT_-FAULT: X1.44
BAT_-ON: X1.38
BAT_TEMP: X1.47
BEACON_-FAULT: X1.30
BEACON_OFF: X1.24
BEACON_SCL: X1.37
BEACON_SDA: X1.39
BUS_CS: X1.27
COMMS_-FAULT: X1.32
COMMS_OFF: X1.25
COMMS_SCL: X1.41
COMMS_SDA: X1.43
GND: C1.2, R1.P$1 (1), X1.1, X1.2, X1.51, X1.52; also elsewhere on the board
LED_-FAULT: X1.28; also elsewhere on the board
LED_OFF: X1.23; also elsewhere on the board
LED_SCL: X1.33; also elsewhere on the board
LED_SDA: X1.35; also elsewhere on the board
OBC_-FAULT: X1.34
OBC_OFF: X1.26
PANELTEMP_SCL: X1.29
PANELTEMP_SDA: X1.31
SCCHG_EN: X1.21
SCOUT_-PG: X1.50
SCOUT_EN: X1.22
SC_-ON: X1.40
SC_-PFO: X1.48
SOLAR_-ON: X1.36
SOLAR_CS1: X1.15
SOLAR_CS2: X1.14
SOLAR_CS3: X1.17
SOLAR_CS4: X1.16
SOLAR_CS5: X1.18
STRUT_GND: C1.1, H4.B3,2, R1.P$2 (2)
SUPERCAP_TEMP: X1.49
VBAT: X1.11, X1.12
VBUS: X1.7, X1.8, X1.9, X1.10; also elsewhere on the board
VSOLAR: X1.3, X1.4, X1.5, X1.6

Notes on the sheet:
Disconnect VSUPERCAP here as EPS provides measurement signal to OBC
Do Not Place Comp! Only for the EPS
OPEN SOURSE SATELLITE INITIATIVE
http://opensat.cc

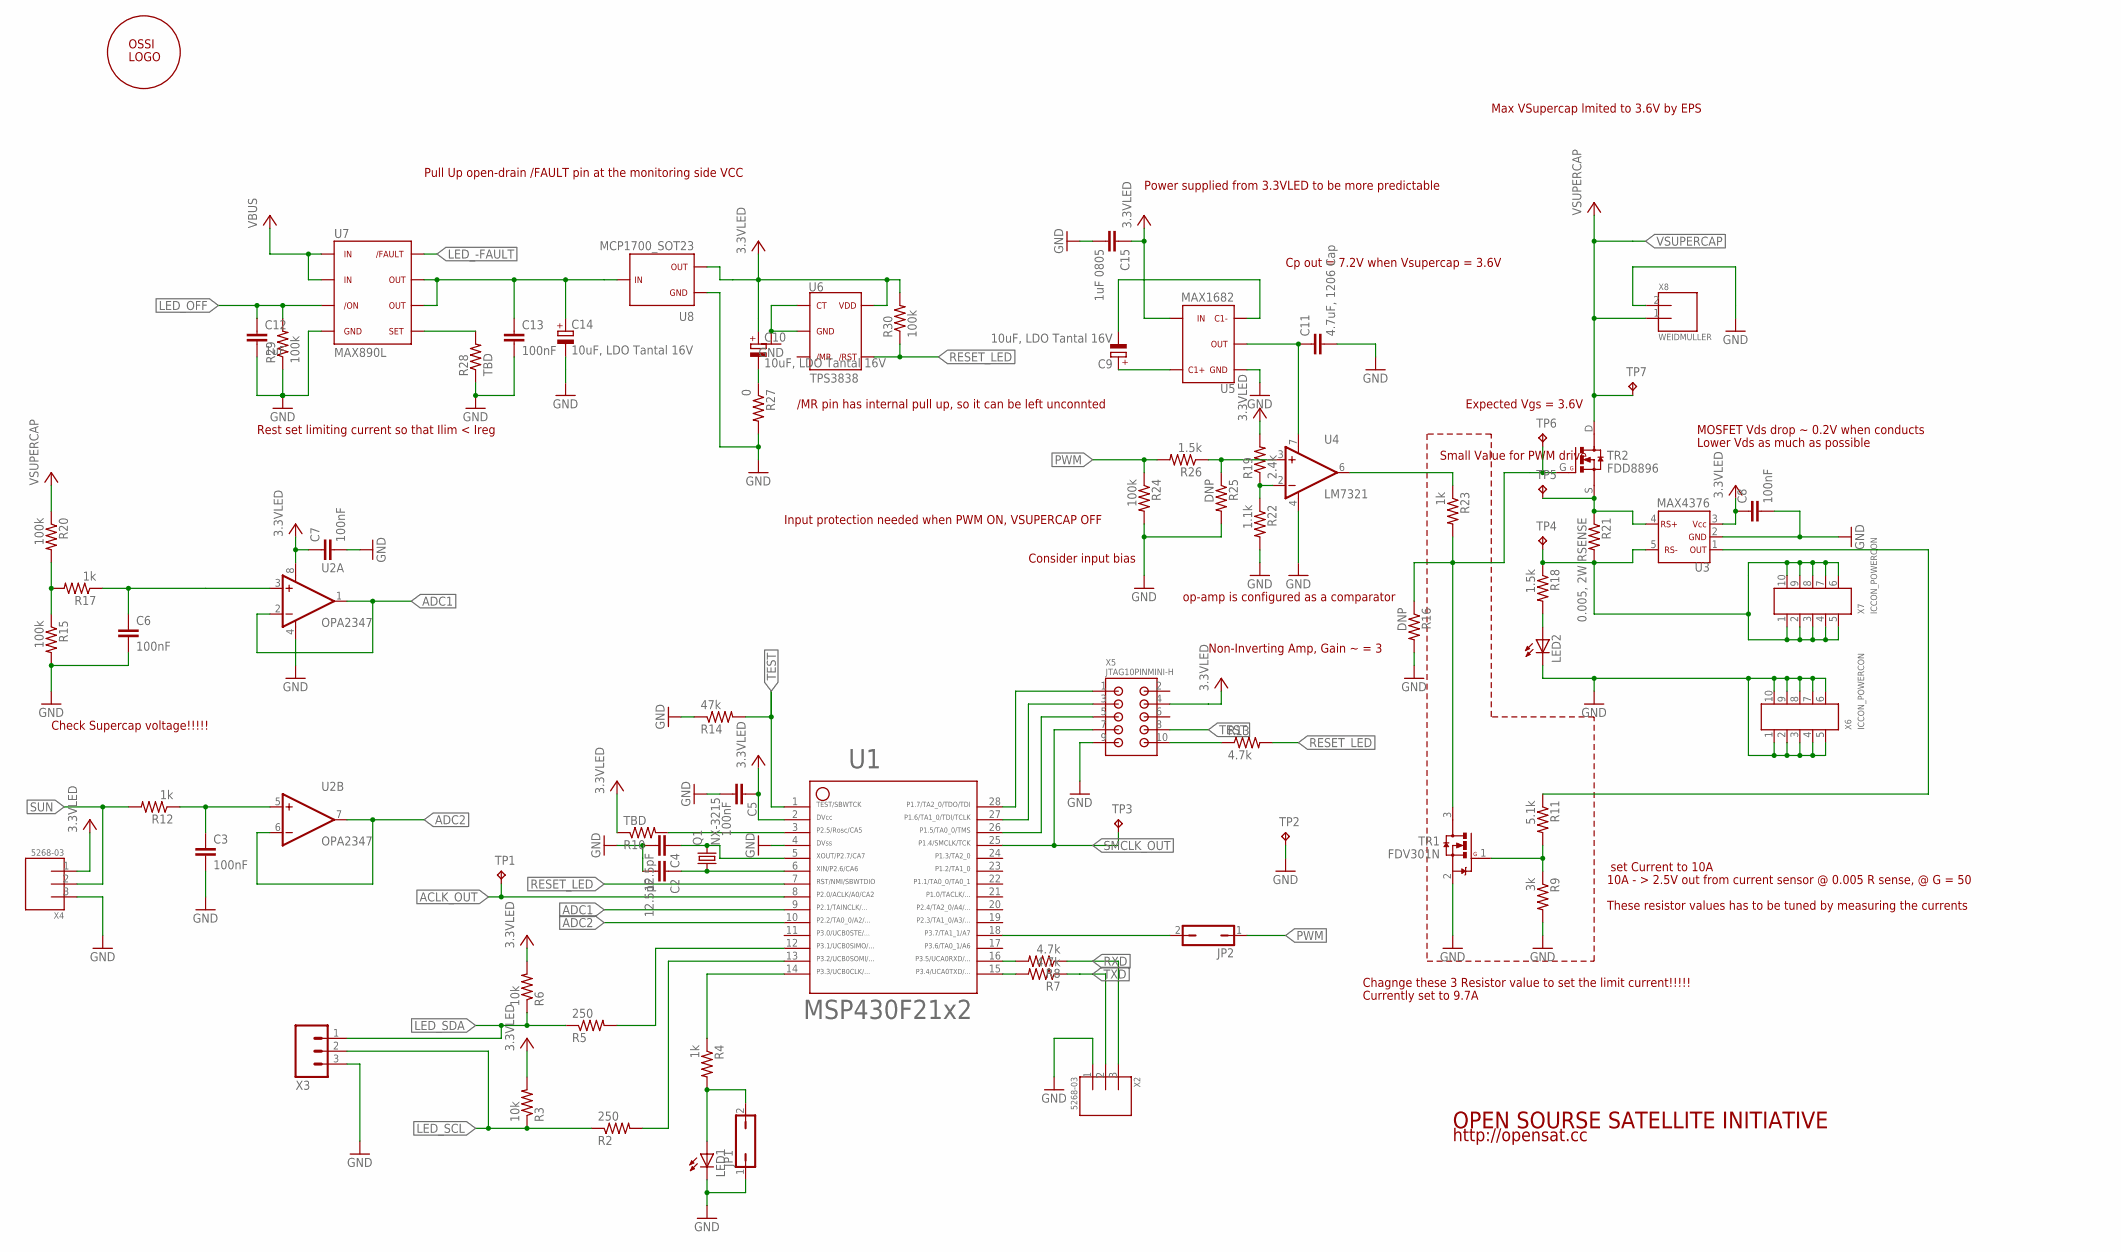
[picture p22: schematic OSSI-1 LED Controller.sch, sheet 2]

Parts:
C2, C4: 12.5pF; C0603(1608)
C3, C5, C6, C7, C8, C13: 100nF; C0603(1608)
C9, C10, C14: 10uF, LDO Tantal 16V; C1206(3216)-A
C11: 4.7uF, 1206 Cap; C1206-GCM31
C12: 1uF; C0603(1608)
C15: 1uF 0805; C0805(2012)
JP1, JP2: JP1Q; JP1
LED1: LED0603; LED-0603
LED2: LEDCHIPLED_0603; CHIPLED_0603
Q1: NX-3215
R2, R5: 250; R0603(1608)
R3, R6: 10k; R0603(1608)
R4, R12, R17, R23: 1k; R0603(1608)
R7, R8, R13: 4.7k; R0603(1608)
R9: 3k; R0603(1608)
R10, R28: TBD; R0603(1608)
R11: 5.1k; R0603(1608)
R14: 47k; R0603(1608)
R15, R20, R24, R29, R30: 100k; R0603(1608)
R16, R25: DNP; R0603(1608)
R18, R26: 1.5k; R0603(1608)
R19: 2.4k; R0603(1608)
R21: 0.005, 2W RSENSE; R4527(12070)
R22: 1.1k; R0603(1608)
R27: 0; R0603(1608)
TP1, TP2, TP3, TP4, TP5, TP6, TP7: TP; TP-13
TR1: FDV301N; SOT23
TR2: FDD8896; TO252
U1: MSP430F2132; PW28
U2: OPA2347; SOT23-8DCN
U3: MAX4376; SOT23-5DBV
U4: LM7321; SO8
U5: MAX1682; SOT23-5DBV
U6: TPS3838; SOT23-5DBV
U7: MAX890L; SO8
U8: MCP1700_SOT23; SOT23
U$: OSSILOGORECT; OSSILOGORECT1005
X2, X4: 5268-03
X3: M03PTH; 1X03
X5: JTAG10PINMINI-H; M50-3200545
X6, X7: ICCON_POWERCON; ICCON6643220-1
X8: WEIDMULLER; WEIDMULLER1760490000

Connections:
3.3VLED: C5.1, C7.1, C8.1, C10.1 (+), C15.1, R3.2, R6.2, R10.1, R19.2, R30.2, U1.2, U2.8 (V+), U3.3, U5.4, U6.5, U8.2, X4.1, X5.4
ACLK_OUT: TP1.TP, U1.8
ADC1: U1.9, U2.1 (OUT), U2.2 (-IN)
ADC2: U1.10, U2.6 (-IN), U2.7 (OUT)
GND: C2.2, C3.2, C4.2, C5.2, C6.2, C7.2, C8.2, C11.P$2 (2), C12.2, C13.2, C14.2 (-), C15.2, JP1.1, LED1.C, LED2.C, R9.2, R14.1, R15.2, R16.2, R22.2, R24.2, R25.2, R27.2, R28.1, R29.1, TP2.TP, TR1.2 (S), U1.4, U2.4 (V-), U3.2, U4.4 (V-), U5.1, U6.1, U6.2, U7.4, U8.1, X2.1, X3.3, X4.3, X5.9, X6.1, X6.2, X6.3, X6.4, X6.5, X6.6, X6.7, X6.8, X6.9, X6.10, X8.2; also elsewhere on the board
LED_-FAULT: U7.8; also elsewhere on the board
LED_OFF: C12.1, R29.2, U7.3; also elsewhere on the board
LED_SCL: R2.1, R3.1, X3.2; also elsewhere on the board
LED_SDA: R5.1, R6.1, X3.1; also elsewhere on the board
unnamed: U1.28, X5.1
unnamed: R10.2, U1.3
unnamed: C13.1, C14.1 (+), U7.6, U7.7, U8.3
unnamed: R16.1, R23.2, TP6.TP, TR1.3 (D), TR2.G
unnamed: C6.1, R17.1, U2.3 (+IN)
unnamed: C3.1, R12.1, U2.5 (+IN)
unnamed: R25.1, R26.1, U4.3 (+IN)
unnamed: R28.2, U7.5
unnamed: R15.1, R17.2, R20.2
unnamed: R18.1, R21.P$2 (2), TP4.TP, U3.5, X7.1, X7.2, X7.3, X7.4, X7.5, X7.6, X7.7, X7.8, X7.9, X7.10
unnamed: C11.P$1 (1), U4.7 (V+), U5.2
unnamed: R23.1, U4.6 (OUT)
unnamed: U1.27, X5.3
unnamed: R21.P$1 (1), TP5.TP, TR2.S, U3.4
unnamed: C10.2 (-), R27.1
unnamed: R19.1, R22.1, U4.2 (-IN)
unnamed: C4.1, Q1.2, U1.5
unnamed: C2.1, Q1.1, U1.6
unnamed: JP1.2, LED1.A, R4.2
unnamed: R5.2, U1.12
unnamed: R2.2, U1.13
unnamed: R11.1, U3.1
unnamed: R4.1, U1.14
unnamed: C9.2 (-), U5.3
unnamed: C9.1 (+), U5.5
unnamed: R8.2, U1.16
unnamed: LED2.A, R18.2
unnamed: R9.1, R11.2, TR1.1 (G)
unnamed: U1.26, X5.5
unnamed: R13.1, X5.10
unnamed: JP2.2, U1.18
unnamed: R7.2, U1.15
PWM: JP2.1, R24.1, R26.2
RESET_LED: R13.2, R30.1, U1.7, U6.4
RXD: R8.1, X2.3
SMCLK_OUT: TP3.TP, U1.25, X5.7
SUN: R12.2, X4.2
TEST: R14.2, U1.1, X5.8
TXD: R7.1, X2.2
VBUS: U7.1, U7.2; also elsewhere on the board
VSUPERCAP: R20.1, TP7.TP, TR2.D, X8.1

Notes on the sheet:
Rest set limiting current so that Ilim < Ireg
Pull Up open-drain /FAULT pin at the monitoring side VCC
/MR pin has internal pull up, so it can be left unconnted
Check Supercap voltage!!!!!
Non-Inverting Amp, Gain ~ = 3
set Current to 10A
10A - > 2.5V out from current sensor @ 0.005 R sense, @ G = 50
Chagnge these 3 Resistor value to set the limit current!!!!!
Expected Vgs = 3.6V
Max VSupercap lmited to 3.6V by EPS
Cp out = 7.2V when Vsupercap = 3.6V
Input protection needed when PWM ON, VSUPERCAP OFF
Currently set to 9.7A
op-amp is configured as a comparator
Power supplied from 3.3VLED to be more predictable
These resistor values has to be tuned by measuring the currents
Small Value for PWM drive
MOSFET Vds drop ~ 0.2V when conducts
Lower Vds as much as possible
Consider input bias
OPEN SOURSE SATELLITE INITIATIVE
http://opensat.cc

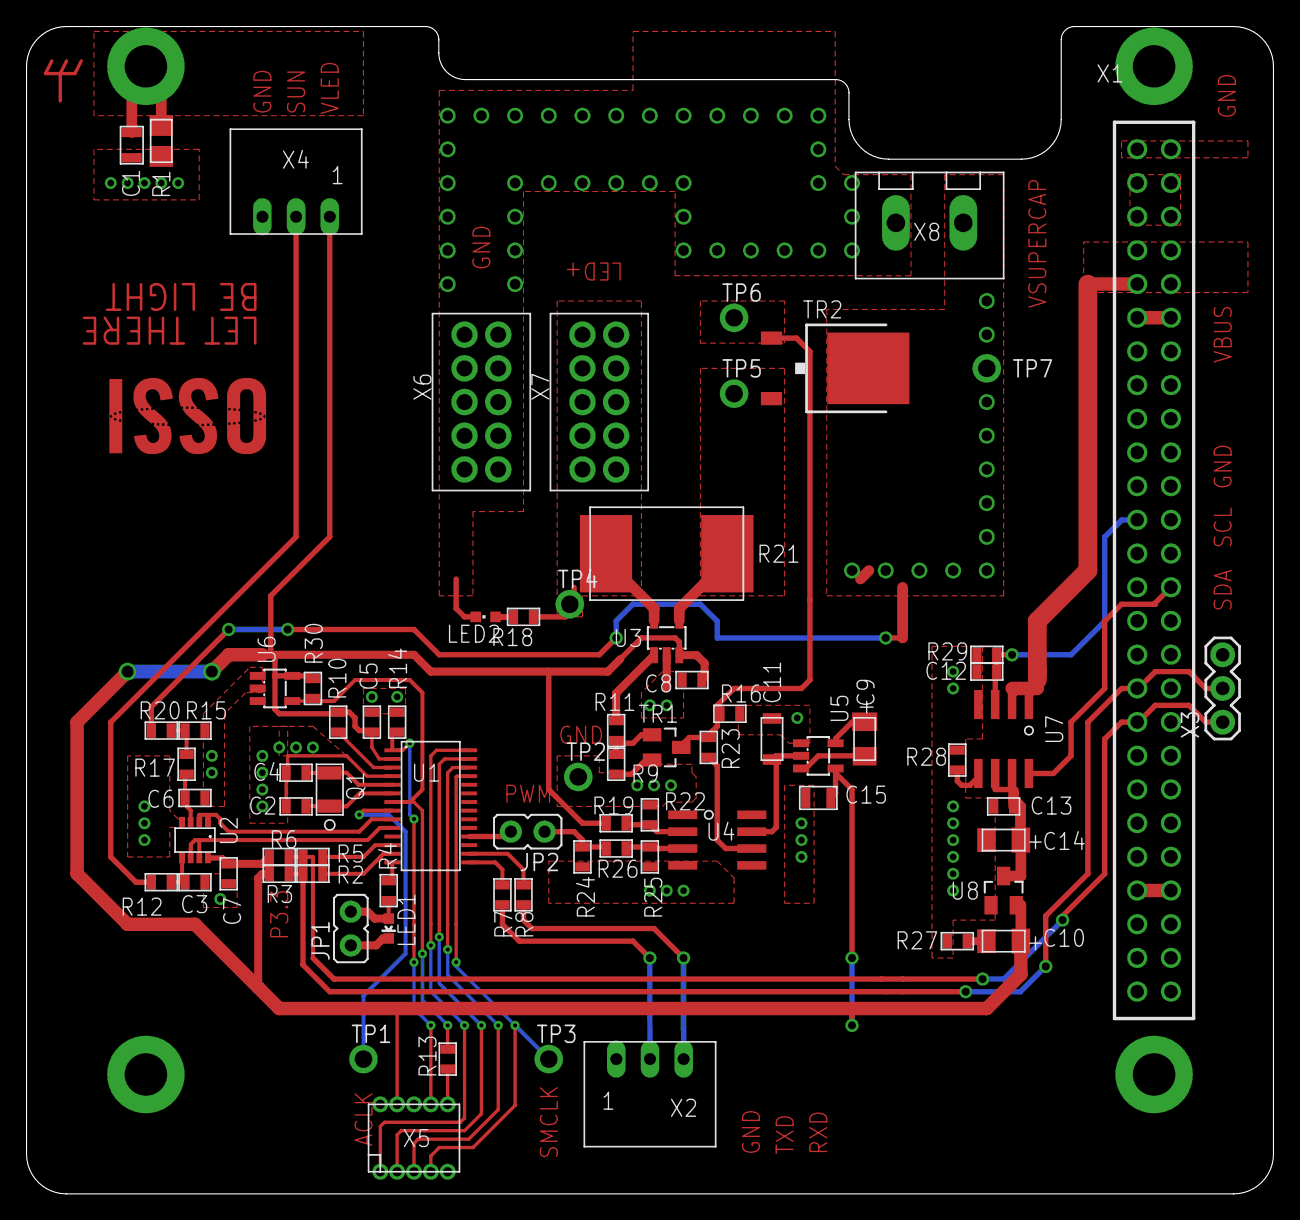
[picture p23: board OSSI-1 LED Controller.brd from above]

Board: 2 copper layers, 94.0 x 88.0 mm, 80 parts (0 on the bottom side), 54 nets.

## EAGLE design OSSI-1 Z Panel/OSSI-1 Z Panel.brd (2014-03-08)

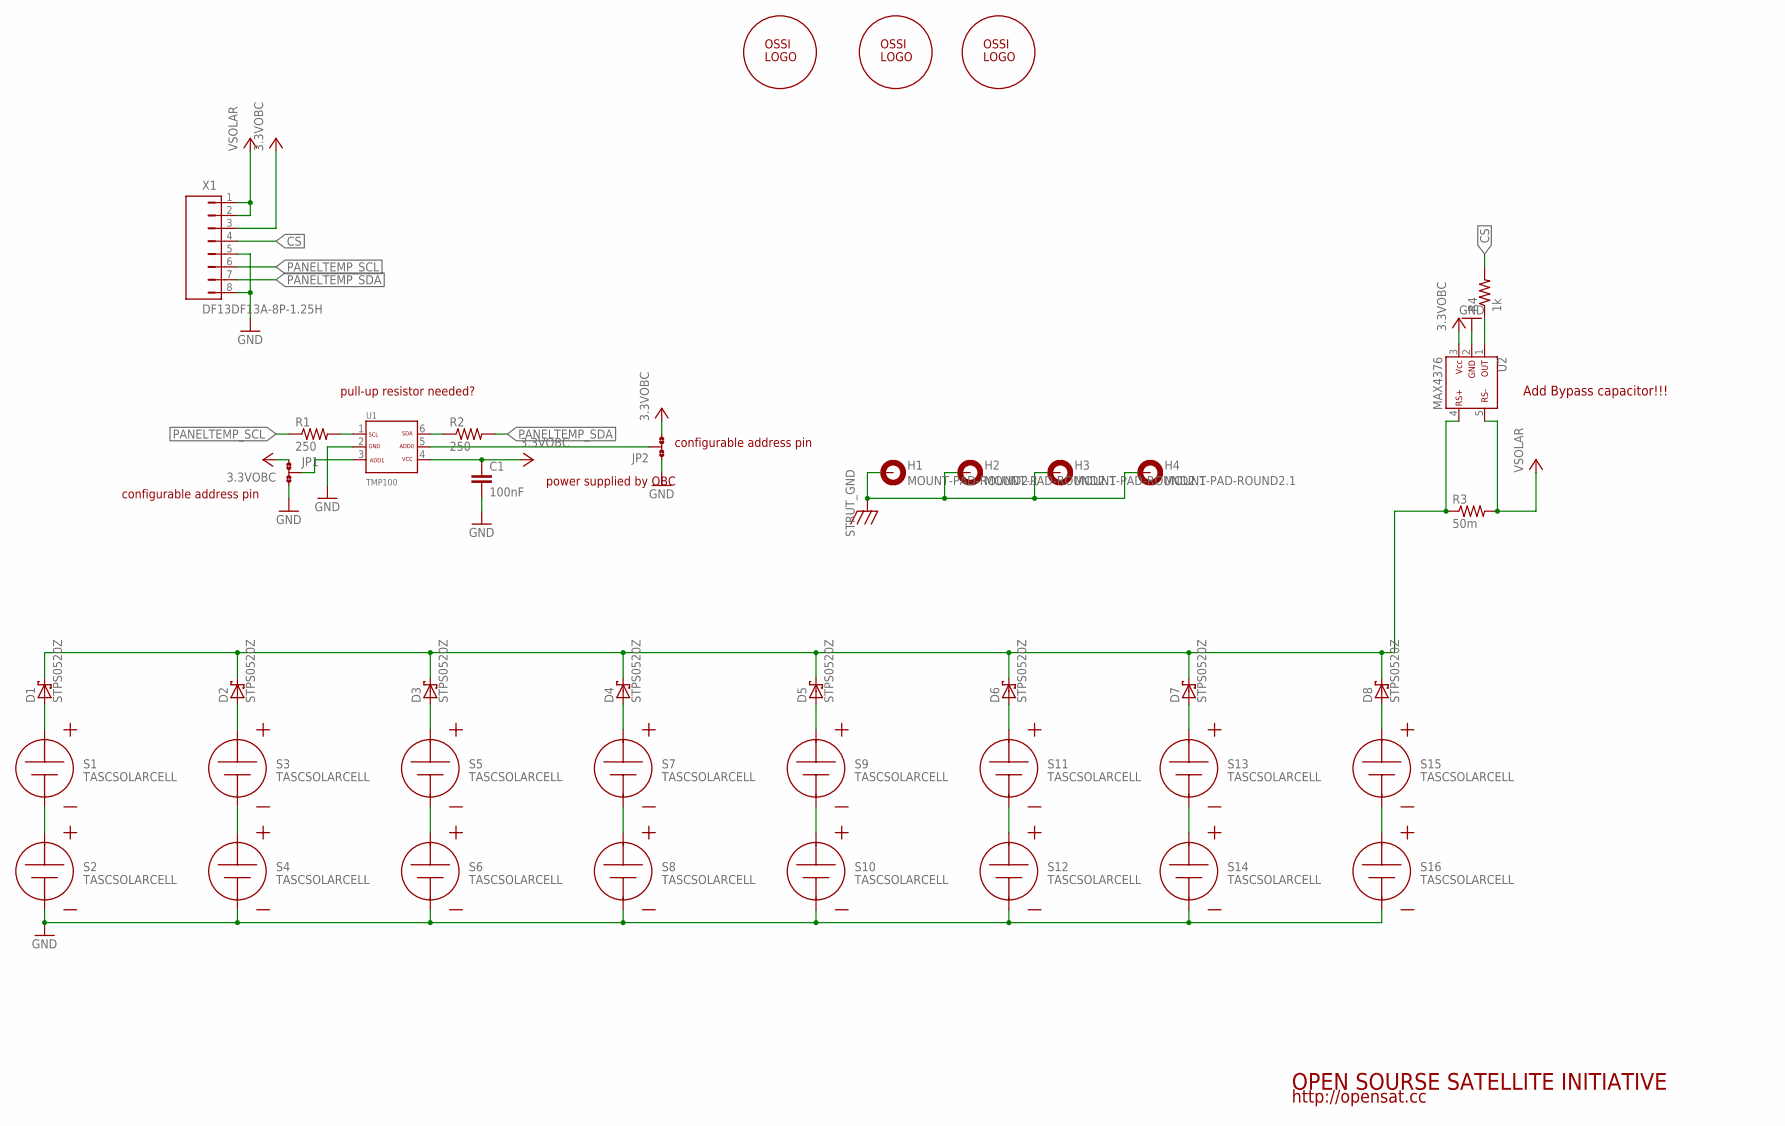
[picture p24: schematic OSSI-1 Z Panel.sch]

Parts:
C1: 100nF; C0603(1608)
D1, D2, D3, D4, D5, D6, D7, D8: STPS0520Z; SOD-123
H1, H2, H3, H4: MOUNT-PAD-ROUND2.1; 2.1-PAD-ROUND
JP1, JP2: JP2; JP2SMD0603
R1, R2: 250; R0603(1608)
R3: 50m; WSL1206
R4: 1k; R0603(1608)
S1, S2, S3, S4, S5, S6, S7, S8, S9, S10, S11, S12, S13, S14, S15, S16: TASCSOLARCELL
U1: TMP100; SOT23-6DBV
U2: MAX4376; SOT23-5DBV
U$1, U$2: OSSILOGO-10; OSSILOGO1010
U$3: OSSITAGCC; CCLOGO
X1: DF13DF13A-8P-1.25H; DF13A-8P

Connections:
3.3VOBC: C1.1, JP1.1, JP2.3, U1.4, U2.3, X1.3
CS: R4.2, X1.4
GND: C1.2, JP1.3, JP2.1, S2.N, S4.N, S6.N, S8.N, S10.N, S12.N, S14.N, S16.N, U1.2, U2.2, X1.5, X1.8
unnamed: S1.N, S2.P
unnamed: D1.A, S1.P
unnamed: S3.N, S4.P
unnamed: D2.A, S3.P
unnamed: S5.N, S6.P
unnamed: D3.A, S5.P
unnamed: S7.N, S8.P
unnamed: D4.A, S7.P
unnamed: S9.N, S10.P
unnamed: D5.A, S9.P
unnamed: S11.N, S12.P
unnamed: D6.A, S11.P
unnamed: S13.N, S14.P
unnamed: D7.A, S13.P
unnamed: S15.N, S16.P
unnamed: D8.A, S15.P
unnamed: R1.2, U1.1
unnamed: R2.1, U1.6
unnamed: D1.C, D2.C, D3.C, D4.C, D5.C, D6.C, D7.C, D8.C, R3.P$1 (1), U2.4
unnamed: JP1.2, U1.3
unnamed: JP2.2, U1.5
unnamed: R4.1, U2.1
PANELTEMP_SCL: R1.1, X1.6
PANELTEMP_SDA: R2.2, X1.7
STRUT_GND: H1.B3,2, H2.B3,2, H3.B3,2, H4.B3,2
VSOLAR: R3.P$2 (2), U2.5, X1.1, X1.2

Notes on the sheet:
configurable address pin
pull-up resistor needed?
power supplied by OBC
Add Bypass capacitor!!!
OPEN SOURSE SATELLITE INITIATIVE
http://opensat.cc

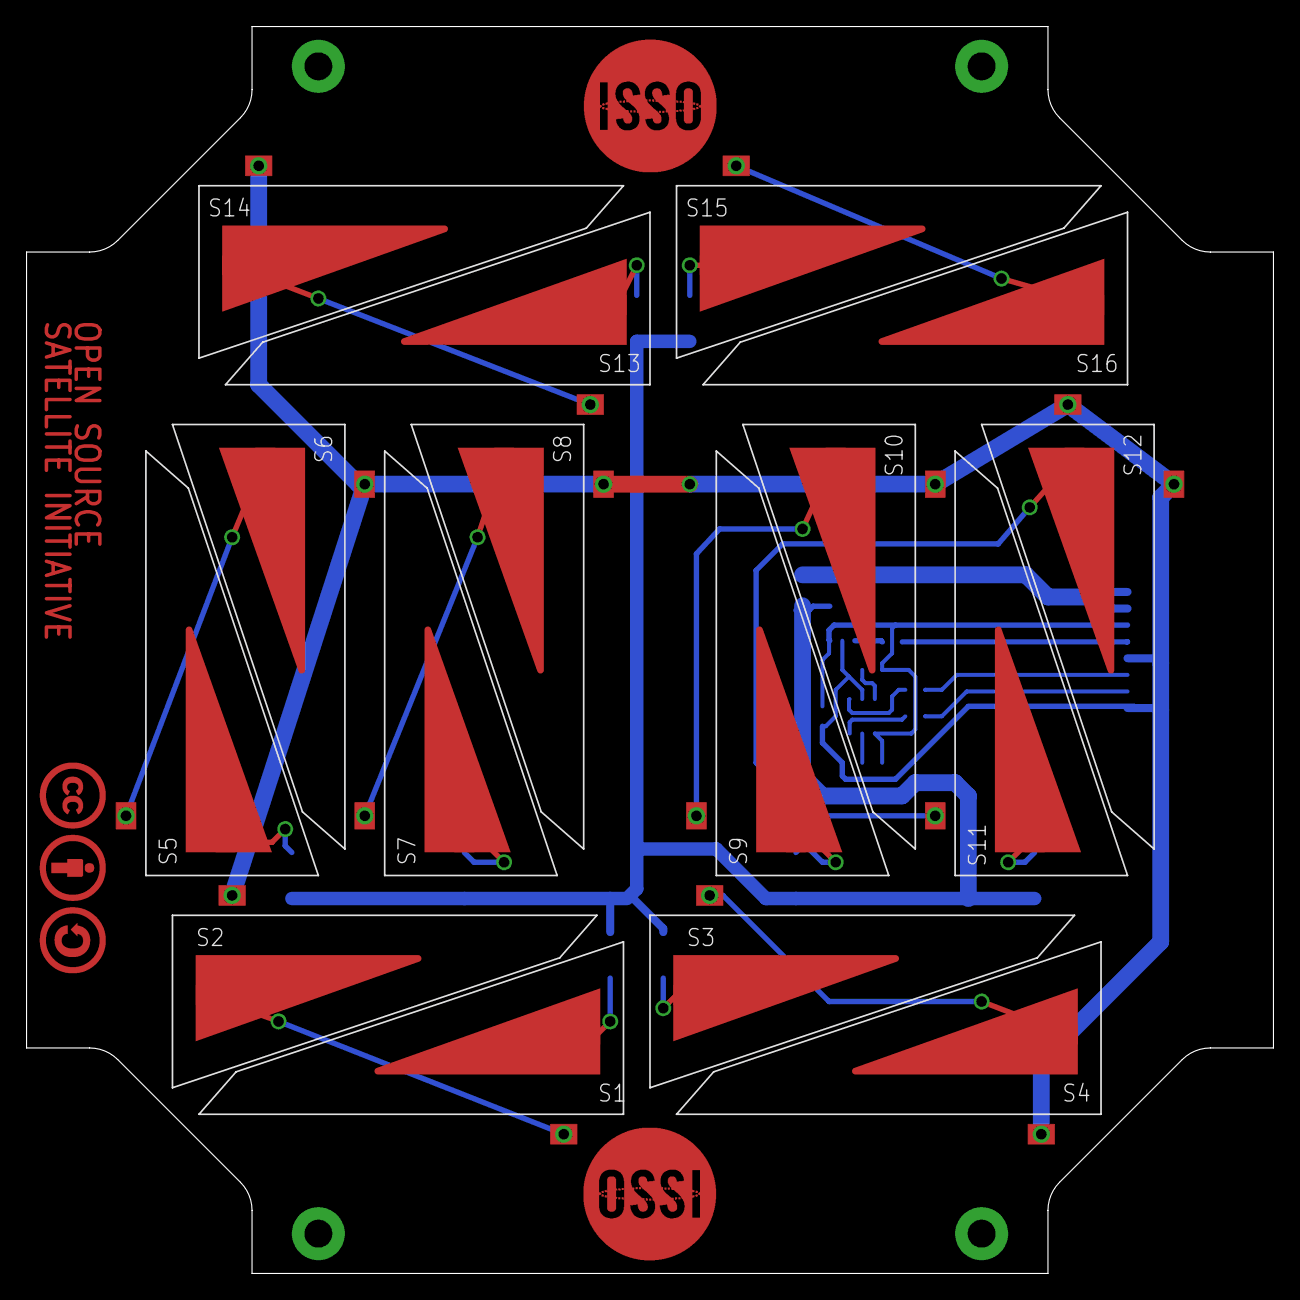
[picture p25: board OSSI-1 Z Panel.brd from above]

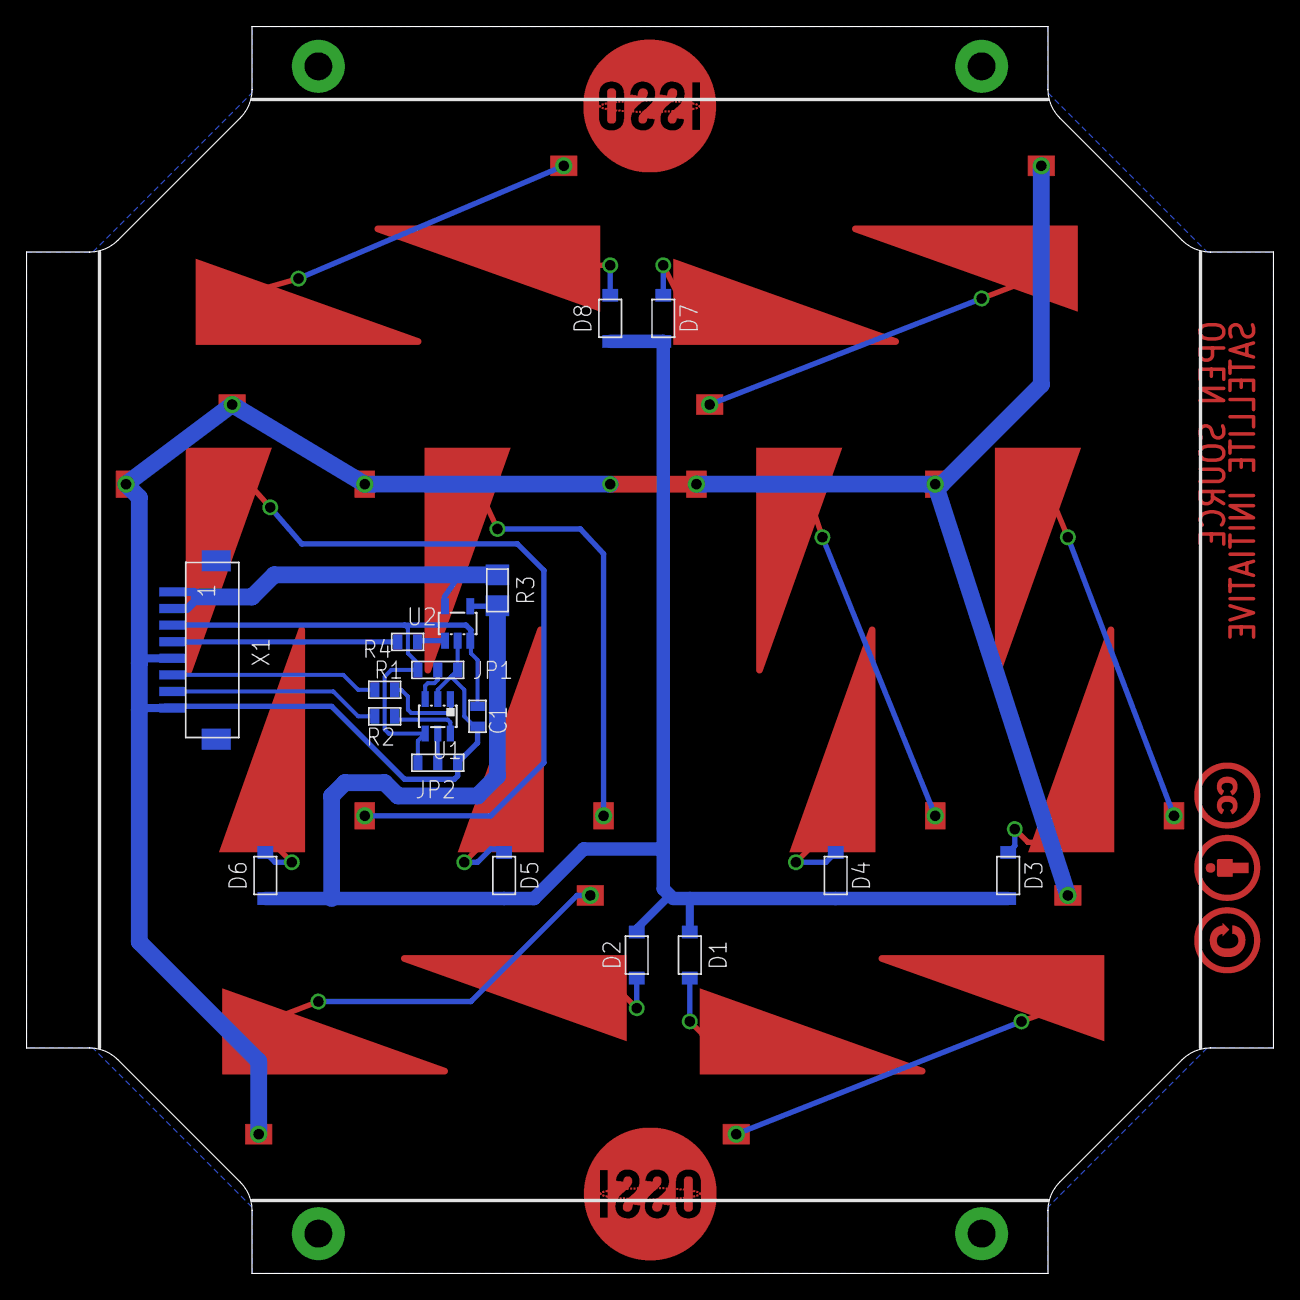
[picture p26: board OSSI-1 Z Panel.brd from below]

Board: 2 copper layers, 94.0 x 94.0 mm, 41 parts (18 on the bottom side), 29 nets.

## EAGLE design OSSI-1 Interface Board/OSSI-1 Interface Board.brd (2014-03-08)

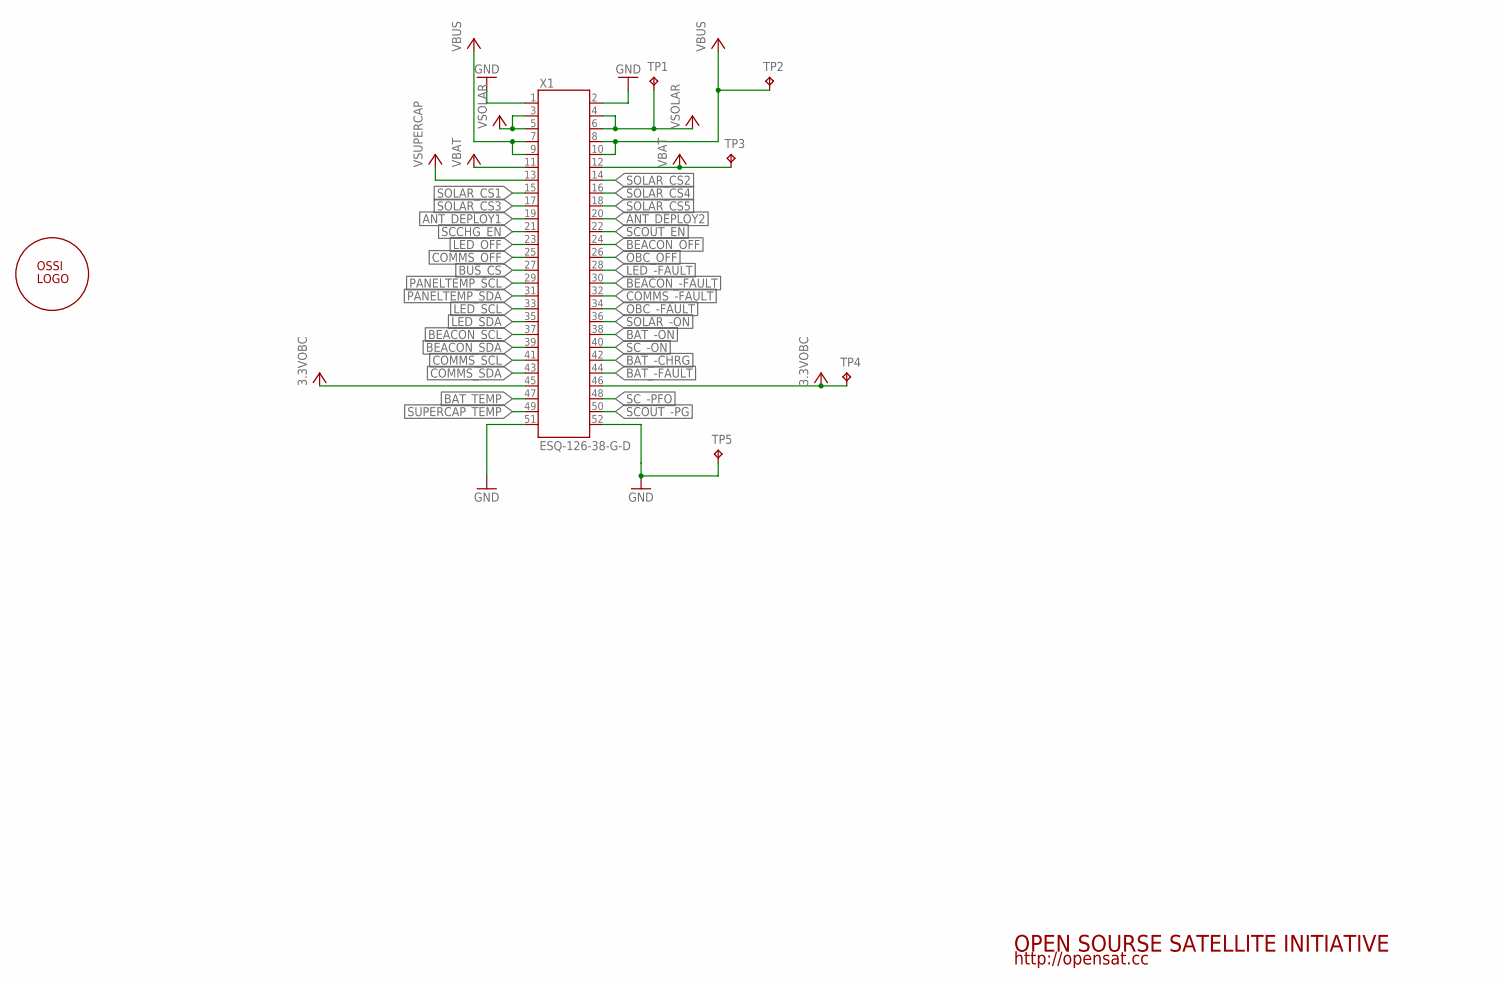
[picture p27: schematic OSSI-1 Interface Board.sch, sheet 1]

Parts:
TP1, TP2, TP3, TP4, TP5: TP; TP-13
U$1: OSSILOGO-10; OSSILOGO1010
X1: ESQ-126-38-G-D; ESQ-126-XX-X-D

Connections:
3.3VOBC: TP4.TP, X1.45, X1.46; also elsewhere on the board
ANT_DEPLOY1: X1.19
ANT_DEPLOY2: X1.20
BAT_-CHRG: X1.42
BAT_-FAULT: X1.44
BAT_-ON: X1.38
BAT_TEMP: X1.47
BEACON_-FAULT: X1.30
BEACON_OFF: X1.24
BEACON_SCL: X1.37
BEACON_SDA: X1.39
BUS_CS: X1.27
COMMS_-FAULT: X1.32
COMMS_OFF: X1.25
COMMS_SCL: X1.41
COMMS_SDA: X1.43
GND: TP5.TP, X1.1, X1.2, X1.51, X1.52; also elsewhere on the board
LED_-FAULT: X1.28
LED_OFF: X1.23
LED_SCL: X1.33
LED_SDA: X1.35
OBC_-FAULT: X1.34
OBC_OFF: X1.26
PANELTEMP_SCL: X1.29; also elsewhere on the board
PANELTEMP_SDA: X1.31; also elsewhere on the board
SCCHG_EN: X1.21
SCOUT_-PG: X1.50
SCOUT_EN: X1.22
SC_-ON: X1.40
SC_-PFO: X1.48
SOLAR_-ON: X1.36
SOLAR_CS1: X1.15; also elsewhere on the board
SOLAR_CS2: X1.14; also elsewhere on the board
SOLAR_CS3: X1.17; also elsewhere on the board
SOLAR_CS4: X1.16; also elsewhere on the board
SOLAR_CS5: X1.18; also elsewhere on the board
SUPERCAP_TEMP: X1.49
VBAT: TP3.TP, X1.11, X1.12
VBUS: TP2.TP, X1.7, X1.8, X1.9, X1.10
VSOLAR: TP1.TP, X1.3, X1.4, X1.5, X1.6; also elsewhere on the board
VSUPERCAP: X1.13

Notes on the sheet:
OPEN SOURSE SATELLITE INITIATIVE
http://opensat.cc

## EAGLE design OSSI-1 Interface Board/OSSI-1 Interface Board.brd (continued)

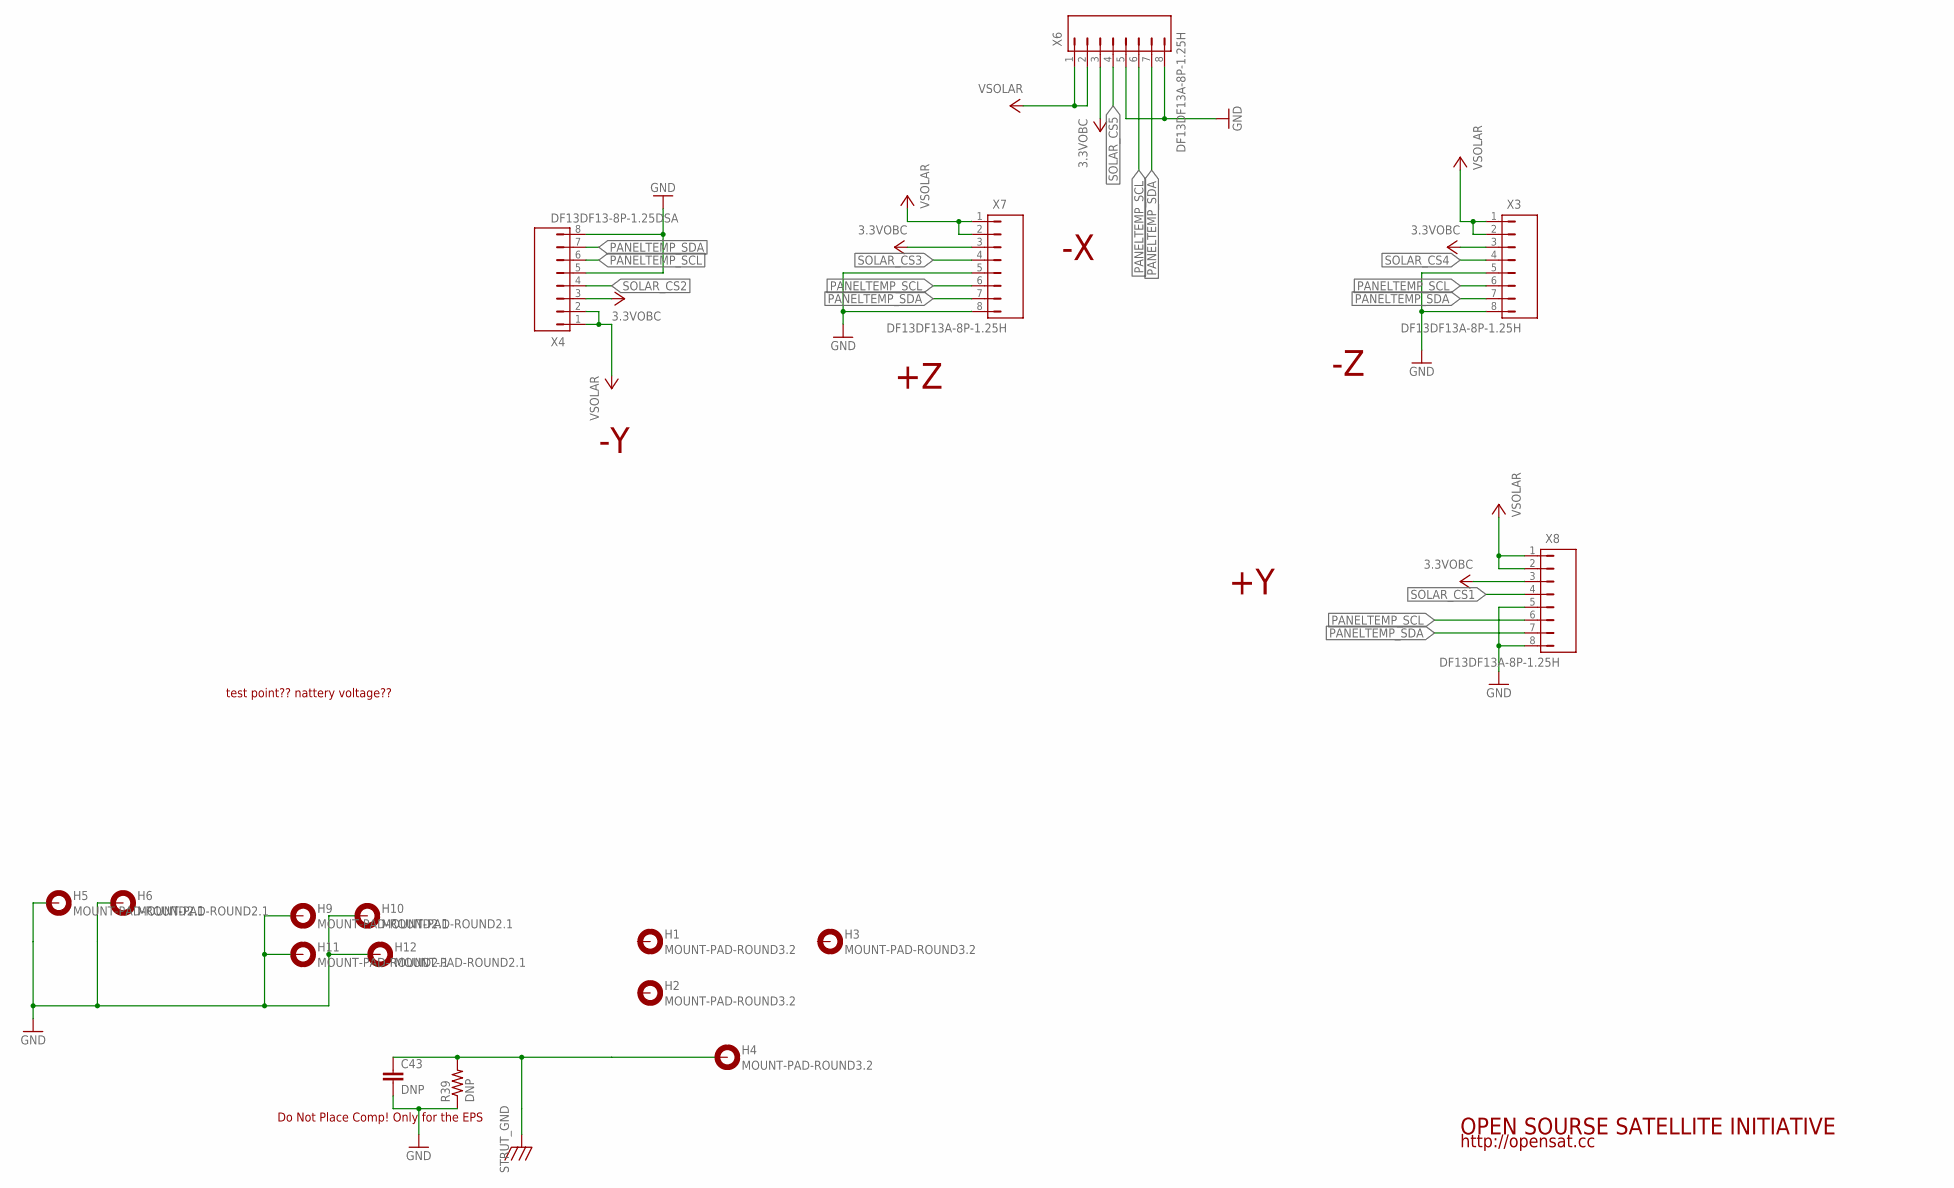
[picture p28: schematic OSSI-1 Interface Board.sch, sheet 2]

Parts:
C43: DNP; C0805(2012)
H1, H2, H3, H4: MOUNT-PAD-ROUND3.2; 3.2-PAD-ROUND
H5, H6, H9, H10, H11, H12: MOUNT-PAD-ROUND2.1; 2.1-PAD-ROUND
R39: DNP; WSL1206
X3, X6, X7, X8: DF13DF13A-8P-1.25H; DF13A-8P
X4: DF13DF13-8P-1.25DSA; DF13-8P-1.25DSA

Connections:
3.3VOBC: X3.3, X4.3, X6.3, X7.3, X8.3; also elsewhere on the board
GND: C43.2, H5.B3,2, H6.B3,2, H9.B3,2, H10.B3,2, H11.B3,2, H12.B3,2, R39.P$1 (1), X3.5, X3.8, X4.5, X4.8, X6.5, X6.8, X7.5, X7.8, X8.5, X8.8; also elsewhere on the board
PANELTEMP_SCL: X3.6, X4.6, X6.6, X7.6, X8.6; also elsewhere on the board
PANELTEMP_SDA: X3.7, X4.7, X6.7, X7.7, X8.7; also elsewhere on the board
SOLAR_CS1: X8.4; also elsewhere on the board
SOLAR_CS2: X4.4; also elsewhere on the board
SOLAR_CS3: X7.4; also elsewhere on the board
SOLAR_CS4: X3.4; also elsewhere on the board
SOLAR_CS5: X6.4; also elsewhere on the board
STRUT_GND: C43.1, H4.B3,2, R39.P$2 (2)
VSOLAR: X3.1, X3.2, X4.1, X4.2, X6.1, X6.2, X7.1, X7.2, X8.1, X8.2; also elsewhere on the board

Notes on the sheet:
test point?? nattery voltage??
Do Not Place Comp! Only for the EPS
OPEN SOURSE SATELLITE INITIATIVE
http://opensat.cc

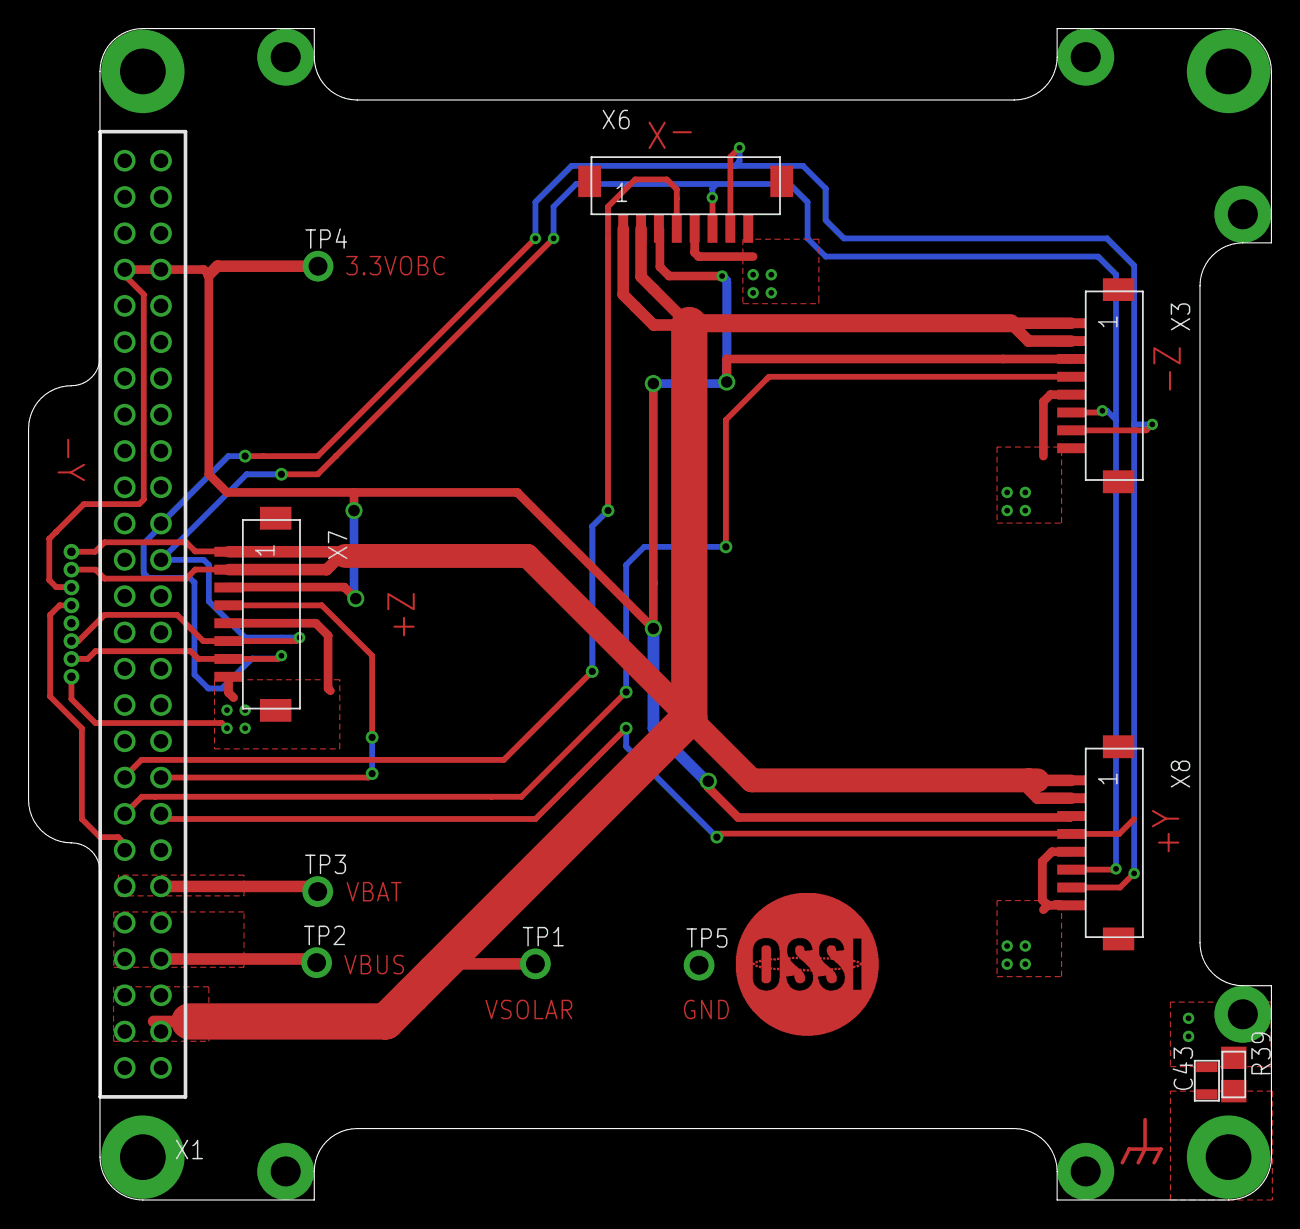
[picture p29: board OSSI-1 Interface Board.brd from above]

Board: 2 copper layers, 87.0 x 82.0 mm, 24 parts (1 on the bottom side), 13 nets.

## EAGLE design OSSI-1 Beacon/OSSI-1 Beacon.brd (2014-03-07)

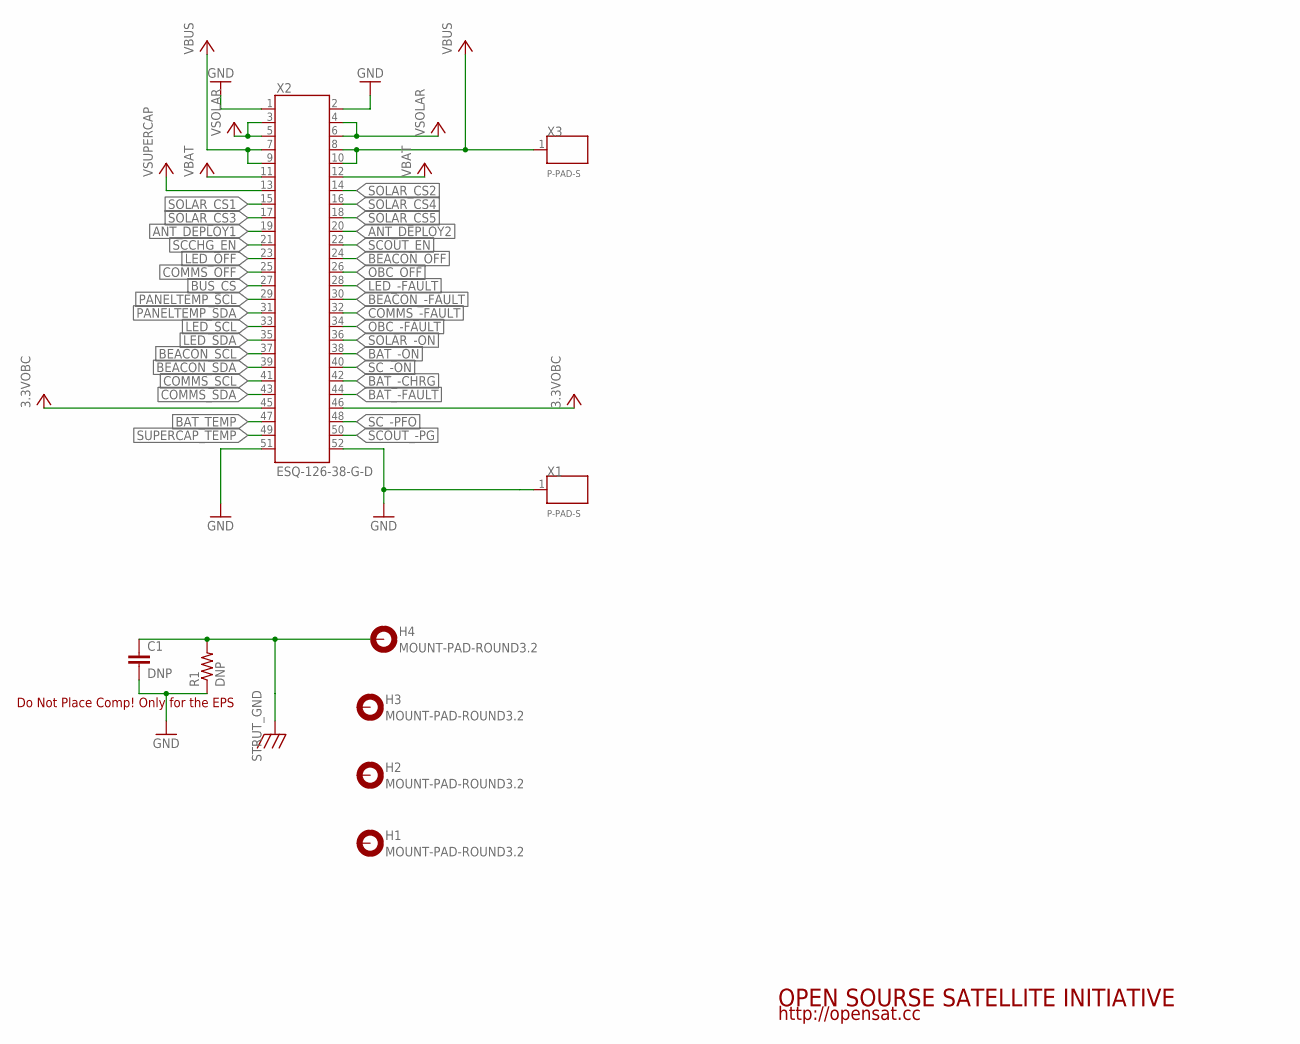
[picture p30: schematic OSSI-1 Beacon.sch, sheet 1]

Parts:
C1: DNP; C0805(2012)
H1, H2, H3, H4: MOUNT-PAD-ROUND3.2; 3.2-PAD-ROUND
R1: DNP; WSL1206
X1, X3: P-PAD-S
X2: ESQ-126-38-G-D; ESQ-126-XX-X-D

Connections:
3.3VOBC: X2.45, X2.46
ANT_DEPLOY1: X2.19
ANT_DEPLOY2: X2.20
BAT_-CHRG: X2.42
BAT_-FAULT: X2.44
BAT_-ON: X2.38
BAT_TEMP: X2.47
BEACON_-FAULT: X2.30; also elsewhere on the board
BEACON_OFF: X2.24; also elsewhere on the board
BEACON_SCL: X2.37; also elsewhere on the board
BEACON_SDA: X2.39; also elsewhere on the board
BUS_CS: X2.27; also elsewhere on the board
COMMS_-FAULT: X2.32
COMMS_OFF: X2.25
COMMS_SCL: X2.41
COMMS_SDA: X2.43
GND: C1.2, R1.P$1 (1), X1.1, X2.1, X2.2, X2.51, X2.52; also elsewhere on the board
LED_-FAULT: X2.28
LED_OFF: X2.23
LED_SCL: X2.33
LED_SDA: X2.35
OBC_-FAULT: X2.34
OBC_OFF: X2.26
PANELTEMP_SCL: X2.29
PANELTEMP_SDA: X2.31
SCCHG_EN: X2.21
SCOUT_-PG: X2.50
SCOUT_EN: X2.22
SC_-ON: X2.40
SC_-PFO: X2.48
SOLAR_-ON: X2.36
SOLAR_CS1: X2.15
SOLAR_CS2: X2.14
SOLAR_CS3: X2.17
SOLAR_CS4: X2.16
SOLAR_CS5: X2.18
STRUT_GND: C1.1, H4.B3,2, R1.P$2 (2)
SUPERCAP_TEMP: X2.49
VBAT: X2.11, X2.12
VBUS: X2.7, X2.8, X2.9, X2.10, X3.1; also elsewhere on the board
VSOLAR: X2.3, X2.4, X2.5, X2.6
VSUPERCAP: X2.13

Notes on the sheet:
Do Not Place Comp! Only for the EPS
OPEN SOURSE SATELLITE INITIATIVE
http://opensat.cc


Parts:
C2, C3, C5: 10nF; C0603(1608)
C4: 0R; C0603(1608)
C6, C10: 100nF; C0603(1608)
C7: 1uF,0805; C0805(2012)
C8: 22uF,1210; C1210-GCM32
C9: 1uF; C0603(1608)
F1: LFCN-160; LFCN
L1: 470nH, 1008 size; L1008(2520)
R2, R4, R5: 100k; R0603(1608)
R3: 6.2k; R0603(1608)
TR1: FDV301N; SOT23
U1: ADL5530; LFCSP8_CP
U2: MAX890L; SO8
X4: RFCON-MCX-R/A; MCX-R/A

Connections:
3.3VBEACON: R5.2; also elsewhere on the board
BEACON_RFOUT: C2.1; also elsewhere on the board
GND: C5.2, C6.2, C7.2, C8.P$2 (2), C9.2, C10.2, F1.2, F1.4, R2.1, R3.1, TR1.2 (S), U1.1, U1.3, U1.4, U1.5, U1.6, U1.8, U2.4, X4.2, X4.3, X4.4, X4.5; also elsewhere on the board
unnamed: C9.1, R4.1, TR1.3 (D), U2.3
unnamed: R3.2, U2.5
unnamed: C2.2, U1.2
unnamed: C3.1, L1.P$2 (2), U1.7
unnamed: C3.2, F1.1
unnamed: C4.1, F1.3
unnamed: C4.2, X4.1
PA_-FAULT: R5.1, U2.8; also elsewhere on the board
PA_ON: R2.2, TR1.1 (G); also elsewhere on the board
VBEACON_PA: C5.1, C6.1, C7.1, C8.P$1 (1), C10.1, L1.P$1 (1), U2.6, U2.7
VBUS: R4.2, U2.1, U2.2; also elsewhere on the board

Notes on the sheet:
Capacitors!!!!!
PA Off by default
Current limited to 220mA
DC blocking cap is added on Front panel
OPEN SOURSE SATELLITE INITIATIVE
http://opensat.cc


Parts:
C11, C13, C28: 22pF; C0603(1608)
C12: 39pF; C0603(1608)
C14, C16: 1nF; C0603(1608)
C15: 10nF; C0603(1608)
C17: 2.2uF, 0805; C0805(2012)
C18, C22: 100pF; C0603(1608)
C19: 1uF; C0603(1608)
C20: 1uF,0603 Too Small!!; C0603(1608)
C21: DNP; C0603(1608)
C23: 1uF 0805; C0805(2012)
C24: 1uF,0603; C0603(1608)
C25: 22nF; C0603(1608)
C26: 68pF; C0603(1608)
C27: 1000pF; C0603(1608)
L2, L3: 68nH; L0603(1608)
L4: 8.2nH; L0603(1608)
L5: 470nH, 1008 size; L1008(2520)
R6: 0; R0603(1608)
R7: 1M; R0603(1608)
R8: 3.6k; R0603(1608)
R9: 2.4k; R0603(1608)
R10: 5.1k; R0603(1608)
TCXO1: 19.2MHz; TCXO_M532
U3: NC7SZ04; SC70-5
U4: ADF7012; TSSOP24

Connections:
BEACON_CE: U4.14 (CE); also elsewhere on the board
BEACON_DATA: U4.4 (TXDATA); also elsewhere on the board
BEACON_MUXOUT: U4.6 (MUXOUT); also elsewhere on the board
BEACON_RFOUT: C13.2, L3.2; also elsewhere on the board
BEACON_SCLK: U4.11 (CLK); also elsewhere on the board
BEACON_SDATA: U4.12 (DATA); also elsewhere on the board
BEACON_SLE: U4.13 (LE); also elsewhere on the board
BEACON_TXCLK: U4.5 (TXCLK); also elsewhere on the board
GND: C11.1, C12.1, C13.1, C15.2, C17.1, C18.2, C19.2, C20.2, C22.2, C23.1, C24.2, C26.1, C28.2, R8.1, R9.2, TCXO1.1, TCXO1.2, U3.3, U4.7 (DGND), U4.19 (RFGND), U4.22 (AGND); also elsewhere on the board
unnamed: L4.1, U4.16 (L2)
unnamed: L4.2, U4.15 (L1)
unnamed: C23.2, C25.1, U4.24 (CREG2)
unnamed: C25.2, U4.17 (CVCO)
unnamed: R8.2, U4.23 (RSET)
unnamed: C27.1, R9.1
unnamed: C14.2, L5.P$2 (2), U4.20 (RFOUT)
unnamed: C28.1, R10.1, U4.18 (VCOIN)
unnamed: C17.2, U4.2 (CREG1)
unnamed: C26.2, C27.2, R10.2, U4.3 (CPOUT)
unnamed: C18.1, C19.1, L5.P$1 (1), R6.2, U4.21 (DVDD_2)
unnamed: C11.2, C14.1, L2.1
unnamed: C12.2, L2.2, L3.1
unnamed: C16.2, C21.1, R7.2, U3.2
unnamed: C16.1, TCXO1.3
OSC1: C21.2, U4.8 (OSC1)
OSC2: R7.1, U3.4, U4.9 (OSC2)
VCCRF: C15.1, C20.1, C22.1, C24.1, R6.1, TCXO1.4, U3.5, U4.1 (DVDD_1); also elsewhere on the board

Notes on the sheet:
tune L4 for for better PLL margin
Clock signal on Y is a bit distored
External inductor is tuned to 8.2nH
with 8.2nH, PLL lock for all vco bias and adj are observed
TCXO signal is needed to be boosted via NC7SZ04 to feed OSC input of ADF7012
OPEN SOURSE SATELLITE INITIATIVE
http://opensat.cc


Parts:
C29, C31, C33, C35, C36, C38, C43: 100nF; C0603(1608)
C30: TBD; C0603(1608)
C32, C34: 12.5pF; C0603(1608)
C37: 1uF; C0603(1608)
C39, C40: 10uF, LDO Tantal 16V; C1206(3216)-A
C41: 10nF; C0603(1608)
C42: 22uF,1210; C1210-GCM32
D1: BAT54S; SOT23
JP1: JP1Q; JP1
L6: 7 R Ferrite Bead, 3A; L0805(2012)
LED1: LED0603; LED-0603
Q1: NX-3215
R11: 47k; R0603(1608)
R12, R19, R20, R22, R23, R24, R25, R26, R27, R28, R31: 4.7k; R0603(1608)
R13, R16: 250; R0603(1608)
R14, R18, R30: 10k; R0603(1608)
R15: 1k; R0603(1608)
R17, R21, R32, R35, R36: 100k; R0603(1608)
R29: DNP; R0603(1608)
R33: 0; R0603(1608)
R34: 23.7k; R0603(1608)
TP1: TP; TP-13
U5: MAX6369; SOT23-8
U6: MSP430F2132; PW28
U7: OPA2347; SOT23-8DCN
U8: TPS3838; SOT23-5DBV
U9: MAX890L; SO8
U10: MCP1700_SOT23; SOT23
U$1: OSSILOGORECT; OSSILOGORECT1005
X5: 5268-02; 5628-02
X6: M03PTH; 1X03
X7: 5268-03
X8: JTAG10PINMINI-H; M50-3200545

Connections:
3.3VBEACON: C35.1, C36.1, C40.1 (+), C41.1, C42.P$1 (1), D1.2 (C2), L6.1, R14.2, R18.2, R36.2, U5.4, U5.5, U5.6, U5.8, U6.2, U7.8 (V+), U8.5, U10.2, X5.1, X8.4; also elsewhere on the board
ADC0: U6.8, U7.6 (-IN), U7.7 (OUT)
ADC1: U6.9, U7.1 (OUT), U7.2 (-IN)
BEACON_-FAULT: U9.8; also elsewhere on the board
BEACON_CE: R22.2; also elsewhere on the board
BEACON_CWCONTROL: R11.1, R12.2, X5.2
BEACON_DATA: R28.2; also elsewhere on the board
BEACON_MUXOUT: R26.2; also elsewhere on the board
BEACON_OFF: C37.1, R35.2, U9.3; also elsewhere on the board
BEACON_SCL: R13.1, R14.1, X6.2; also elsewhere on the board
BEACON_SCLK: R25.2; also elsewhere on the board
BEACON_SDA: R16.1, R18.1, X6.1; also elsewhere on the board
BEACON_SDATA: R24.2; also elsewhere on the board
BEACON_SLE: R23.2; also elsewhere on the board
BEACON_TXCLK: R27.2; also elsewhere on the board
BEACON_WDT_RST: C31.1, U5.7, U8.3
BUS_CS: R30.1; also elsewhere on the board
GND: C29.2, C30.2, C31.2, C32.2, C33.2, C34.2, C35.2, C36.2, C37.2, C38.2, C39.2 (-), C41.2, C42.P$2 (2), C43.2, D1.1 (A1), JP1.1, LED1.C, R11.2, R17.2, R29.2, R32.2, R33.2, R34.1, R35.1, TP1.TP, U5.2, U6.4, U7.4 (V-), U8.1, U8.2, U9.4, U10.1, X6.3, X7.1, X8.9; also elsewhere on the board
unnamed: R15.1, U6.11
unnamed: U6.27, X8.3
unnamed: U6.26, X8.5
unnamed: U6.25, X8.7
unnamed: C34.1, Q1.2, U6.5
unnamed: C32.1, Q1.1, U6.6
unnamed: JP1.2, LED1.A, R15.2
unnamed: U6.28, X8.1
unnamed: R16.2, U6.12
unnamed: R13.2, U6.13
unnamed: R20.2, U6.16
unnamed: U5.1, U6.10
unnamed: C29.1, D1.3 (C1A2), R12.1, U6.14
unnamed: C30.1, R17.1, R21.2, U7.5 (+IN)
unnamed: R31.1, X8.10
unnamed: R34.2, U9.5
unnamed: C33.1, R29.1, R30.2, U7.3 (+IN)
unnamed: R19.2, U6.15
unnamed: C40.2 (-), R33.1
unnamed: R28.1, U6.24
unnamed: R27.1, U6.23
unnamed: R26.1, U6.22
unnamed: R25.1, U6.21
unnamed: R24.1, U6.20
unnamed: R23.1, U6.19
unnamed: R22.1, U6.18
unnamed: C38.1, C39.1 (+), U9.6, U9.7, U10.3
PA_-FAULT: U6.3; also elsewhere on the board
PA_ON: U6.17; also elsewhere on the board
RESETBEACON: R31.2, R36.1, U6.7, U8.4
RXD: R20.1, X7.3
TEST: R32.1, U6.1, X8.8
TXD: R19.1, X7.2
VBUS: R21.1, U9.1, U9.2; also elsewhere on the board
VCCRF: C43.1, L6.2; also elsewhere on the board

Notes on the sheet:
Rest set limiting current so that Ilim < Ireg
Pull Up open-drain /FAULT pin at the monitoring side VCC
Max Current: 1.2A
Ref1: Poly Sat paper
Ref2: Pumpkin Co. Cubesat kit
/MR pin has internal pull up, so it can be left unconnted
use board's power
DIGITAL / RF POWER CHOKE
Pull Down resistor!!
Check TVS influences on OpAmp Input
Conntect Test Pin to JTAG!!
current limited to 58.2mA
for SW connecting
OPEN SOURSE SATELLITE INITIATIVE
http://opensat.cc


Board: 2 copper layers, 92.0 x 92.0 mm, 116 parts (1 on the bottom side), 83 nets.

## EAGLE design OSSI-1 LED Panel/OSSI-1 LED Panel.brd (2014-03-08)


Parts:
LED1, LED2, LED3, LED4: LED-P7; P7
X1, X2: P-PAD

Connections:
LED+: LED1.A, LED2.A, LED3.A, LED4.A, X1.1
LED-: LED1.C, LED2.C, LED3.C, LED4.C, X2.1

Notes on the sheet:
OPEN SOURSE SATELLITE INITIATIVE
http://opensat.cc

Board: 2 copper layers, 6 parts (0 on the bottom side), 2 nets, no tracks yet.

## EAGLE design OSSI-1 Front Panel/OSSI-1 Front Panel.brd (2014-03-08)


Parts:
ADS1: OSSIADS
C1, C2: 5.975pF; C0805(2012)
L1, L2: 22.4nH; L0805(2012)
L3: 6mm dia, 5 turn; 0207/10
LD1: TEMT6000X01; TEMT6000-SEN
R1: 10k; R0805(2012)
X1, X2: RFCON-MCX-V; MCX-V
X3, X4, X5, X11: P-PAD-S
X6, X7, X8, X9, X10: P-PAD

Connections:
3.3VOBC: LD1.COLLECTOR (C1), X5.1
ADS_1A: ADS1.1A, X9.1
ADS_2A: ADS1.2A, X10.1
COMMS_N: C2.1, L1.2, X8.1
COMMS_P: C1.1, L2.1, X7.1
GND: ADS1.1B, ADS1.2B, C2.2, L2.2, L3.2, R1.1, X1.2, X1.3, X1.4, X1.5, X2.2, X2.3, X2.4, X2.5, X3.1
LED_SUNSENSOR: LD1.EMITTER (E1), R1.2, X4.1
unnamed: L3.1, X6.1
unnamed: X1.1, X11.1
unnamed: C1.2, L1.1, X2.1

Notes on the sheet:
LC Balun
0603HC_22NX coilcraft is used
6pF is used
UHF
VHF
Antenna Deployment System
Connect 12pF ceramic Cap from the L3 to GND
12pF cap connected to 1 turn from X6 and Ground
OPEN SOURSE SATELLITE INITIATIVE
http://opensat.cc

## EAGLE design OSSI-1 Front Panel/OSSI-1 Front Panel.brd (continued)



Board: 2 copper layers, 109.5 x 82.5 mm, 19 parts (14 on the bottom side), 10 nets.

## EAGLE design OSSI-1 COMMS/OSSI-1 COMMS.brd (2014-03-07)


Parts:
H1, H2, H3, H4: MOUNT-PAD-ROUND3.2; 3.2-PAD-ROUND
TP1: TP; TP-13
X1: ESQ-126-38-G-D; ESQ-126-XX-X-D

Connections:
3.3VOBC: X1.45, X1.46
ANT_DEPLOY1: X1.19
ANT_DEPLOY2: X1.20
BAT_-CHRG: X1.42
BAT_-FAULT: X1.44
BAT_-ON: X1.38
BAT_TEMP: X1.47
BEACON_-FAULT: X1.30
BEACON_OFF: X1.24
BEACON_SCL: X1.37
BEACON_SDA: X1.39
BUS_CS: X1.27
COMMS_-FAULT: X1.32; also elsewhere on the board
COMMS_OFF: X1.25; also elsewhere on the board
COMMS_SCL: X1.41; also elsewhere on the board
COMMS_SDA: X1.43; also elsewhere on the board
GND: TP1.TP, X1.1, X1.2, X1.51, X1.52; also elsewhere on the board
LED_-FAULT: X1.28
LED_OFF: X1.23
LED_SCL: X1.33
LED_SDA: X1.35
OBC_-FAULT: X1.34; also elsewhere on the board
OBC_OFF: X1.26; also elsewhere on the board
PANELTEMP_SCL: X1.29
PANELTEMP_SDA: X1.31
SCCHG_EN: X1.21
SCOUT_-PG: X1.50
SCOUT_EN: X1.22
SC_-ON: X1.40
SC_-PFO: X1.48
SOLAR_-ON: X1.36
SOLAR_CS1: X1.15
SOLAR_CS2: X1.14
SOLAR_CS3: X1.17
SOLAR_CS4: X1.16
SOLAR_CS5: X1.18
STRUT_GND: H4.B3,2
SUPERCAP_TEMP: X1.49
VBAT: X1.11, X1.12
VBUS: X1.7, X1.8, X1.9, X1.10; also elsewhere on the board
VSOLAR: X1.3, X1.4, X1.5, X1.6
VSUPERCAP: X1.13

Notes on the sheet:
OPEN SOURSE SATELLITE INITIATIVE
http://opensat.cc


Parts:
C1: 6.8pF; C0603(1608)
C2, C5, C16, C17, C23: DNP; C0603(1608)
C3: 13pF; C0603(1608)
C4, C18, C20: 8.2pF; C0603(1608)
C6: 10uF; C1206-GCM31
C7: 470pF 0805; C0805(2012)
C8: 1000pF; C0603(1608)
C9, C10, C15, C25, C26: 56pF; C0603(1608)
C11, C37: 3.3uF; C1210-TMK325
C12, C21: 10pF; C0603(1608)
C13, C31, C33: 1nF; C0603(1608)
C14: 15pF; C0603(1608)
C19: 12pF; C0603(1608)
C22, C24: 6pF; C0603(1608)
C27: 330pF; C0603(1608)
C28, C32, C35, C36, C43: 10nF; C0603(1608)
C29: 100pF; C0603(1608)
C30: 47pF; C0603(1608)
C34, C39, C40, C47: 100nF; C0603(1608)
C38: 180pF; C0603(1608)
C41: 4.7uF; C1210-GCM32
C42: 22uF,1210; C1210-GCM32
C44: 4.7uF,1210; C0805(2012)
C45: 22uF; C1210-GCM32
C46: 100uF; C1210-GCM32
F1: LFCN-530; LFCN
JP1: JP1Q; JP1
L1, L14: 27nH; L0603(1608)
L2, L4: DNP; L0603(1608)
L3, L6, L8, L10: 0R; L0603(1608)
L5: 39nH; L0603(1608)
L7: 0R; LQH32CN331K23L
L9: 1.5nH; L0603(1608)
L11, L12: 11nH; L0603(1608)
L13: 3.9nH; L0603(1608)
L15: 39nH 3012, 1A rating; NR3012
R1, R12, R13, R15: 100k; R0603(1608)
R2, R3, R10, R14: 1.5k; R0603(1608)
R4: 180; R0603(1608)
R5: 11nH; R0603(1608)
R6: 4.12k; R0603(1608)
R7: 470k; R0603(1608)
R8: 15.968k; R0603(1608)
R9: 49.9k; R0603(1608)
R11: 750R; R0603(1608)
R16: 22k; R0603(1608)
TR1: FDV301N; SOT23
U1: MAX2640; SOT23-6
U2: PE4259; SC70-6
U3: RF5110G
U4: OPA347; SOT23-5DBV
U5: MAX869L; 16QSOP
U6: LMZ10503EXT; TO-PMOD-7
X2: RFCON-MCX-R/A; MCX-R/A

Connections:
3.3VCOMMS: R12.1; also elsewhere on the board
COMMSRX_RFIN: C3.1, L1.2; also elsewhere on the board
COMMSRX_RFINB: C1.1, L1.1; also elsewhere on the board
COMMSTX_RFOUT: C24.1, L14.1; also elsewhere on the board
GND: C1.2, C2.2, C5.2, C6.P$2 (2), C7.2, C11.P$2 (2), C12.2, C13.2, C14.2, C16.1, C17.1, C18.2, C19.2, C20.2, C21.2, C22.2, C23.1, C27.2, C28.1, C29.2, C30.2, C31.2, C32.1, C33.2, C34.2, C35.2, C36.1, C37.P$2 (2), C39.2, C40.2, C41.P$2 (2), C42.P$2 (2), C43.2, C44.2, C45.P$2 (2), C46.P$2 (2), C47.2, F1.2, F1.4, L2.2, L4.2, R1.1, R4.1, R7.2, R8.2, R11.1, R13.2, TR1.2 (S), U1.2, U1.3, U1.5, U2.2, U3.2, U3.4, U3.TPAD, U4.2 (V-), U5.8, U6.4, U6.PAD, X2.2, X2.3, X2.4, X2.5; also elsewhere on the board
unnamed: C23.2, C26.2, L10.1
unnamed: L5.1, U1.1
unnamed: C8.1, L5.2
unnamed: C4.2, U1.4
unnamed: C5.1, F1.1, L6.1
unnamed: C8.2, F1.3
unnamed: C9.1, L4.1, L6.2
unnamed: C17.2, L8.1, L10.2
unnamed: C20.1, C25.1, L12.2, R4.2
unnamed: C18.1, C24.2, L11.1
unnamed: C19.1, L11.2, L12.1
unnamed: C15.2, C16.2, L8.2
unnamed: C10.2, U2.5
unnamed: R2.2, U2.4
unnamed: C4.1, L2.1, L3.2
unnamed: R3.1, U2.6
unnamed: C10.1, X2.1
unnamed: C40.1, R15.1, TR1.3 (D), U5.7
unnamed: C43.1, U6.3
unnamed: R10.1, TR1.1 (G)
unnamed: C41.P$1 (1), C42.P$1 (1), U5.2, U5.3, U5.6, U5.11, U5.14, U5.15, U6.1, U6.2
unnamed: R6.2, R8.1, R9.2, U6.5
unnamed: C38.2, R6.1
unnamed: R11.2, U5.9
unnamed: C15.1, U2.1
unnamed: C9.2, U2.3
unnamed: C2.1, C3.2, L3.1
unnamed: C39.1, R14.2, U4.3 (+IN)
unnamed: C21.1, C22.1, C26.1, L13.2
unnamed: L9.2, U3.5, U3.6
unnamed: C25.2, U3.3
unnamed: L13.1, L15.P$1 (1), U3.9, U3.10, U3.11, U3.12
unnamed: JP1.2, U4.1 (OUT)
unnamed: C14.1, L7.P$2 (2), L9.1
unnamed: R5.1, U3.1
PA_-FAULT: R12.2, U5.10
PA_BIAS: R13.1, R14.1, R16.2; also elsewhere on the board
PA_ON: R7.1, R10.2; also elsewhere on the board
TX_ON: R1.2, R2.1; also elsewhere on the board
VAPC: C28.2, C32.2, JP1.1, U3.15, U3.16
VBUS: R15.2, U5.1, U5.4, U5.5, U5.12, U5.13, U5.16; also elsewhere on the board
VCCRF: C6.P$1 (1), C7.1, C29.1, C34.1, L14.2, R3.2, U1.6; also elsewhere on the board
VCOMMS_PA: C11.P$1 (1), C12.1, C13.1, C27.1, C30.1, C31.1, C33.1, C35.1, C36.2, C37.P$1 (1), C38.1, C44.1, C45.P$1 (1), C46.P$1 (1), C47.1, L7.P$1 (1), L15.P$2 (2), R5.2, R9.1, R16.1, U3.14, U4.5 (V+), U6.6, U6.7

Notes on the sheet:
PA Maching
Harmonics Filter
50 Ohm
C value?
Maching
variable capacitor
75 Ohm
LC Balun
post impedance matching
for VAPC of PA
set to 2.8V
Use DAC to change the divider voltage point
0dbm
1Watt
also check 23.7k / 75k combination
important!!
chage this if resistance affects
pull down!!
15.5dB Gain Measured @ these values
15pF / 47nH / 1500pF will give similar results
0 Ohm worked best for us
3.3uF tantal or 4.7uF Ceramic worked OK
Large Capacitor is needed for better power out!!
These setting will affect the whole output power!
Better to have trimmper cap for c21 / c22
Eval board settng is 13nH & 10pF
Set VCOMMS_PA to 3.3~3.4V
Current drive capability should be larger!!!
OPA347 is changed to LM7321 and a jumper wire is used to complete the circuit!!
Set to 2.8V for 1W RF power and best efficiency!!!
Use Tantal for larger RF out
10pF +6pF is better than 16 pF why???
tune RF switch to lower the insertion loss. currently around 1.2 dB loss!!!!
1500pF
47nH
8.2nH
Final Value but the result will be similar
12pF
Set current limit = ~ 1.6A
OPEN SOURSE SATELLITE INITIATIVE


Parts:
C48, C49, C50, C52, C54, C58, C60, C64, C65, C66, C68, C69, C73, C77: 100nF; C0603(1608)
C51, C56, C59, C62, C63, C67, C74, C75, C76, C79: 10nF; C0603(1608)
C53, C70: 100pF; C0603(1608)
C55, C71: 22nF; C0603(1608)
C57, C72: 1.2nF; C0603(1608)
C61, C78: 22pF; C0603(1608)
R17, R23: 3.9; R0603(1608)
R18, R22: 3.6k; R0603(1608)
R19, R24: 1.1k; R0603(1608)
R20, R25: 280; R0603(1608)
R21, R26: 100; R0603(1608)
TCXO1, TCXO2: 19.2MHz; TCXO_M532
U7, U8: ADF7021-N; LFCSP48

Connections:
COMMSRX_CE: U7.24; also elsewhere on the board
COMMSRX_CLK: U7.35; also elsewhere on the board
COMMSRX_CLKOUT: U7.36
COMMSRX_CPOUT: C62.1, R20.2, R21.2, U7.42
COMMSRX_DATA: U7.34; also elsewhere on the board
COMMSRX_MUXOUT: U7.37; also elsewhere on the board
COMMSRX_RFIN: U7.6; also elsewhere on the board
COMMSRX_RFINB: U7.7; also elsewhere on the board
COMMSRX_SCLK: U7.28; also elsewhere on the board
COMMSRX_SDATA: U7.26; also elsewhere on the board
COMMSRX_SLE: U7.25; also elsewhere on the board
COMMSRX_SREAD: U7.27; also elsewhere on the board
COMMSRX_SWD: U7.33; also elsewhere on the board
COMMSRX_TCXO: C61.2, U7.39
COMMSRX_VCOIN: C57.1, R20.1, U7.1
COMMSTX_CE: U8.24; also elsewhere on the board
COMMSTX_CLK: U8.35; also elsewhere on the board
COMMSTX_CLKOUT: U8.36
COMMSTX_CPOUT: C75.1, R25.2, R26.2, U8.42
COMMSTX_DATA: U8.34; also elsewhere on the board
COMMSTX_MUXOUT: U8.37; also elsewhere on the board
COMMSTX_RFOUT: U8.4; also elsewhere on the board
COMMSTX_SCLK: U8.28; also elsewhere on the board
COMMSTX_SDATA: U8.26; also elsewhere on the board
COMMSTX_SLE: U8.25; also elsewhere on the board
COMMSTX_SREAD: U8.27; also elsewhere on the board
COMMSTX_TCXO: C78.2, U8.39
COMMSTX_VCOIN: C72.1, R25.1, U8.1
GND: C48.2, C49.2, C50.2, C51.2, C52.2, C53.2, C56.2, C57.2, C58.2, C59.2, C60.2, C62.2, C63.2, C64.2, C65.2, C66.2, C67.2, C69.2, C70.2, C72.2, C73.2, C74.2, C75.2, C76.2, C77.2, C79.2, R17.1, R18.2, R19.2, R22.1, R23.1, R24.1, TCXO1.1, TCXO1.2, TCXO2.1, TCXO2.2, U7.5, U7.12, U7.19, U7.22, U7.29, U7.45, U7.47, U7.EXP, U8.5, U8.6, U8.7, U8.12, U8.19, U8.22, U8.29, U8.45, U8.47, U8.EXP; also elsewhere on the board
unnamed: C60.1, U7.41
unnamed: C65.1, U8.11
unnamed: C50.1, U7.31
unnamed: C49.1, U7.11
unnamed: C55.1, U7.48
unnamed: R19.1, U7.8
unnamed: R18.1, U7.10
unnamed: C54.2, R17.2
unnamed: C71.1, U8.48
unnamed: R22.2, U8.10
unnamed: C68.2, R23.2
unnamed: R24.2, U8.8
unnamed: C77.1, U8.41
unnamed: C66.1, U8.31
unnamed: C68.1, C71.2, U8.2
unnamed: C54.1, C55.2, U7.2
unnamed: C73.1, R26.1
unnamed: C58.1, R21.1
unnamed: C61.1, TCXO1.3
unnamed: C78.1, TCXO2.3
VCCRF: C48.1, C51.1, C52.1, C53.1, C56.1, C59.1, C63.1, C64.1, C67.1, C69.1, C70.1, C74.1, C76.1, C79.1, TCXO1.4, TCXO2.4, U7.3, U7.9, U7.32, U7.40, U7.43, U8.3, U8.9, U8.32, U8.40, U8.43; also elsewhere on the board

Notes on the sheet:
clkout testpoint
sync word detection eyediagram test?
0.8Vpp out with ac coupled capacitor
22uF added!!
110 is used
OPEN SOURSE SATELLITE INITIATIVE
http://opensat.cc


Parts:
C80, C81: 12.5pF; C0603(1608)
C82, C83, C84, C85, C86, C88, C93: 100nF; C0603(1608)
C87: 1uF; C0603(1608)
C89, C90: 10uF, LDO Tantal 16V; C1206(3216)-A
C91: 10nF; C0603(1608)
C92: 22uF,1210; C1210-GCM32
JP2: JP1Q; JP1
L16: 7R, 3A, Ferrite bead; L0805(2012)
LED1, LED2: LEDCHIPLED_0603; CHIPLED_0603
Q1: NX-3215
R27, R30: 250; R0603(1608)
R28, R29, R33, R34, R35, R40: 4.7k; R0603(1608)
R31, R32: 10k; R0603(1608)
R36: 470k; R0603(1608)
R37: 1.5k; R0603(1608)
R38, R39: 1k; R0603(1608)
R41: 0; R0603(1608)
R42: 6.2k; R0603(1608)
R43, R44: 100k; R0603(1608)
U9: MSP430F1611; PM/PAG64
U10: MAX6369; SOT23-8
U11: TPS3838; SOT23-5DBV
U12: MAX890L; SO8
U13: MCP1700_SOT23; SOT23
U$1: OSSILOGORECT; OSSILOGORECT1005
X3: M03PTH; 1X03
X4, X6: P-PAD-S
X5: 5268-03
X7: JTAG10PINMINI-H; M50-3200545

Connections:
3.3VCOMMS: C84.1, C85.1, C86.1, C90.1 (+), C91.1, C92.P$1 (1), L16.1, R31.2, R32.2, R36.2, R44.2, U9.1, U9.64, U10.4, U10.5, U10.6, U10.8, U11.5, U13.2, X7.4; also elsewhere on the board
/RST: R40.2, R44.1, U9.58, U11.4
COMMSRX_CE: U9.21; also elsewhere on the board
COMMSRX_CLK: R35.2; also elsewhere on the board
COMMSRX_DATA: R34.2; also elsewhere on the board
COMMSRX_MUXOUT: U9.13; also elsewhere on the board
COMMSRX_SCLK: U9.17; also elsewhere on the board
COMMSRX_SDATA: U9.19; also elsewhere on the board
COMMSRX_SLE: U9.20; also elsewhere on the board
COMMSRX_SREAD: U9.18; also elsewhere on the board
COMMSRX_SWD: U9.16; also elsewhere on the board
COMMSTX_CE: U9.37; also elsewhere on the board
COMMSTX_CLK: R28.2; also elsewhere on the board
COMMSTX_DATA: R29.2; also elsewhere on the board
COMMSTX_MUXOUT: U9.22; also elsewhere on the board
COMMSTX_SCLK: U9.25; also elsewhere on the board
COMMSTX_SDATA: U9.27; also elsewhere on the board
COMMSTX_SLE: U9.36; also elsewhere on the board
COMMSTX_SREAD: U9.26; also elsewhere on the board
COMMS_-FAULT: U12.8; also elsewhere on the board
COMMS_-RST: C83.1, U10.7, U11.3
COMMS_OFF: C87.1, R43.2, U12.3; also elsewhere on the board
COMMS_SCL: R30.1, R32.1, X3.2; also elsewhere on the board
COMMS_SDA: R27.1, R31.1, X3.1; also elsewhere on the board
GND: C80.2, C81.2, C82.2, C83.2, C84.2, C85.2, C86.2, C87.2, C88.2, C89.2 (-), C91.2, C92.P$2 (2), C93.2, JP2.2, LED1.C, LED2.C, R41.2, R42.1, R43.1, U9.53, U9.62, U9.63, U10.2, U11.1, U11.2, U12.4, U13.1, X3.3, X5.1, X7.9; also elsewhere on the board
LED1: R39.1, U9.50
unnamed: R40.1, X7.10
unnamed: C81.1, Q1.1, U9.8
unnamed: C80.1, Q1.2, U9.9
unnamed: C88.1, C89.1 (+), U12.6, U12.7, U13.3
unnamed: R42.2, U12.5
unnamed: C82.1, U9.7
unnamed: U9.57, X7.7
unnamed: U9.56, X7.5
unnamed: U9.55, X7.3
unnamed: U9.54, X7.1
unnamed: LED1.A, R38.2
unnamed: R38.1, U9.49
unnamed: JP2.1, LED2.A, R39.2
unnamed: U9.35, X5.3
unnamed: U9.34, X5.2
unnamed: R27.2, U9.29
unnamed: R30.2, U9.31
unnamed: R34.1, U9.15
unnamed: R35.1, U9.14
unnamed: R28.1, U9.23
unnamed: R29.1, U9.24
unnamed: U9.42, U10.1
unnamed: C90.2 (-), R41.1
unnamed: U9.33, X6.1
unnamed: U9.32, X4.1
OBC_-FAULT: R33.2, R36.1; also elsewhere on the board
OBC_-FAULT_IN: R33.1, U9.12
OBC_OFF: R37.2; also elsewhere on the board
OBC_OFF_OUT: R37.1, U9.2
PA_BIAS: U9.5; also elsewhere on the board
PA_ON: U9.40; also elsewhere on the board
RX_ON: U9.39
TX_ON: U9.38; also elsewhere on the board
VBUS: U12.1, U12.2; also elsewhere on the board
VCCRF: C93.1, L16.2; also elsewhere on the board

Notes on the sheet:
/MR pin has internal pull up, so it can be left unconnted
use board's power
DAC
unconnected pins?
Rest set limiting current so that Ilim < Ireg
Pull Up open-drain /FAULT pin at the monitoring side VCC
DIGITAL / RF POWER CHOKE
222.5mA limit
Ground is shared but the ground plane is carefully layouted
OPEN SOURSE SATELLITE INITIATIVE
http://opensat.cc


Board: 2 copper layers, 94.0 x 94.0 mm, 188 parts (1 on the bottom side), 130 nets.

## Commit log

2012-10-20 combining all OSSI-1 electronics related repositories
    [+XPanel.brd, +XPanel.sch, LEDALPanel.brd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]
2012-12-05 ADF7012 based OSSI-1 New Beacon Board project created
    [OSSICommsBeaconNew.brd, OSSICommsBeaconNew.sch]
2012-12-06 MSP430F2132 added / New Beacon Modified
    [OSSIBeacon.brd, OSSIBeacon.sch, OSSICommsBeaconNew.brd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]
2012-12-06 OSSI New Beacon Board Circuit 90% done
    [OSSIBeacon.brd, OSSIBeacon.sch]
2012-12-06 New Beacon board updating
    [OSSIBeacon.brd, OSSIBeacon.sch]
2012-12-07 OSSI New Beacon Almost done
    [OSSIBeacon.brd, OSSIBeacon.sch]
2012-12-10 OSSI New Beacon layout done
    [OSSIBeacon.brd, OSSIBeacon.sch]
2012-12-10 I2C Testboard gerber done / New Beacon gerber done
    [OSSIBeacon.brd, OSSIBeacon.sch, OSSII2CTest.brd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]
2012-12-21 OSSI COMMS PA components value changed based on Swisscube
    [OSSIComms.brd, OSSIComms.sch]
2013-01-24 OSSI Shield Library Added
    [OSSIDevBoard.sch]
2013-01-24 OSSI Dev Board Alpha added
    [OSSIComms.brd, OSSIDevBoard.brd, OSSIDevBoard.sch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]
2013-01-29 EPS comment added to Chassis Structure GND move
    [OSSIEPS.sch]
2013-01-29 2132 based LED controller being made / related lbr updated
    [OSSIBeacon.sch, OSSILEDController2132.brd, OSSILEDController2132.sch]
2013-01-29 MCP1700 SO23 added
    [OSSILEDController2132.brd, OSSILEDController2132.sch]
2013-01-30 Chage EPS StrutGND R size to 1206!!! note added
    [OSSIEPS.sch]
2013-02-05 New OBC being made
    [OSSIOBCNew.brd, OSSIOBCNew.sch, OSSISolarZ.brd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]
2013-02-06 New OBC schematic / board file ok
    [OSSIOBCNew.brd, OSSIOBCNew.sch]
2013-02-06 OSSI OBC New Gerber file added
    [OSSIOBCNew.brd, OSSIOBCNew.sch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]
2013-02-07 New OBC / LTC3105 / LM94022 Board gerber added
    [LM94022TmpBoard.brd, LM94022TmpBoard.sch, LTC3105Board.brd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]
2013-02-07 +Xpanel size changed
    [+XPanel.brd, OSSIOBCNew.brd]
2013-02-10 LTC3105 board notes added
    [LTC3105Board.brd, LTC3105Board.sch]
2013-02-12 comment added
    [LM94022TmpBoard.sch]
2013-02-17 new eps board being added
    [+XPanel.sch, OSSIEPSNew.brd, OSSIEPSNew.sch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]
2013-02-17 eps board almost done
    [OSSIEPSNew.brd]
2013-02-18 battery supercap board added / library added
    [BatterySuperCapBoard.brd, BatterySuperCapBoard.sch, OSSIEPSNew.brd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]
2013-02-18 supercap battery board added
    [BatterySuperCapBoard.brd, BatterySuperCapBoard.sch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]
2013-02-18 led controller board almost done
    [BatterySuperCapBoard.brd, BatterySuperCapBoard.sch, OSSILEDControllerNew.brd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]
2013-02-19 beacon newnew led new
    [OSSIBeaconNewNew.brd, OSSIBeaconNewNew.sch]
2013-02-19 series resistor added
    [OSSIBeaconNewNew.brd, OSSIBeaconNewNew.sch]
2013-02-20 beacon almost done
    [OSSIBeaconNewNew.brd, OSSIBeaconNewNew.sch]
2013-02-20 gerber files are created / led current setting fixed to 9.7A
    [BatterySuperCapBoard.brd, ExtensionBoard.brd, ExtensionBoard.sch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]
2013-02-20 ossi comms new added
    [OSSICommsNew.brd, OSSICommsNew.sch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]
2013-02-21 beta 1 release
    [+XPanel.brd, +XPanelNew.brd, +XPanelNew.sch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]
2013-02-22 schematics renumbered
    [OSSIBeaconNewNew.brd, OSSIBeaconNewNew.sch, OSSICommsNew.brd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]
2013-02-22 LNA gain measured to 15.5dB and R / L values are fixed
    [OSSICommsNew.brd, OSSICommsNew.sch]
2013-02-22 LNA values
    [OSSICommsNew.sch]
2013-02-23 COMMS PA setting fixed!
    [OSSICommsNew.brd, OSSICommsNew.sch]
2013-02-25 beacon valued corrected
    [OSSIBeaconNewNew.brd, OSSIBeaconNewNew.sch]
2013-02-25 beacon value changed
    [OSSIBeaconNewNew.brd, OSSIBeaconNewNew.sch]
2013-02-25 comms names renumbred
    [OSSIBeaconNewNew.sch, OSSICommsNew.brd]
2013-02-25 led controlloer renumbered
    [OSSILEDControllerNew.brd]
2013-02-25 EPS renumbered
    [OSSIEPSNew.brd]
2013-02-25 OBC renumbered
    [OSSIOBCNew.brd, OSSIOBCNew.sch]
2013-03-04 all values for tuned results are updated
    [OSSIBeaconNewNew.brd, OSSIBeaconNewNew.sch, OSSICommsNew.brd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]
2013-03-04 front panel value
    [+XPanelNew.sch]
2013-03-29 comms value
    [OSSIBeaconNewNew.brd, OSSICommsNew.brd, OSSICommsNew.sch]
2013-07-07 some library description updated
    [OSSICommsNew.brd, OSSICommsNew.sch]
2014-03-07 design file are added / missing values are added
    [OSSICommsNew.brd, OSSICommsNew.sch]
2014-03-07 design files are added
    [OSSIBeaconNewNew.brd, OSSIBeaconNewNew.sch]
2014-03-08 design flies are added
    [OSSIEPSNew.brd, OSSIEPSNew.sch]
2014-03-08 led sch updated / design files are added
    [OSSILEDControllerNew.brd, OSSILEDControllerNew.sch]
2014-03-08 temp board file added
    [LM94022TmpBoard.brd, LM94022TmpBoard.sch]
2014-03-08 got rid of old files
    [+XPanel.brd, +XPanel.sch, +XPanelNew.brd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]
2014-03-08 more cleanup
    [+XPanelNew.sch, BatterySuperCapBoard.sch, ExtensionBoard.sch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]
2014-03-11 opa347 setting corrected
    [OSSI-1 COMMS.sch]
2014-03-16 sch corrected
    [OSSI-1 COMMS.sch]
2014-03-18 value comment changed
    [OSSI-1 COMMS.sch]
2014-03-18 tuning power cap commet added
    22uF near the adf7021-n is added for better performance by lowering the
    power noised
    [OSSI-1 COMMS.sch]
2014-03-18 excel file added
    [OSSI-1 COMMS BOM.xlsx]
2014-03-18 bom text file deleted
2014-03-18 excel bom file is added
    [OSSI-1 Beacon BOM.xlsx, OSSI-1 COMMS BOM.xlsx, OSSI-1 EPS BOM.xlsx]
2014-03-18 excel files are added
    [OSSI-1 LED Module BOM.xlsx, OSSI-1 OBC BOM.xlsx, OSSI-1 Side Solar Panel BOM.xlsx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]

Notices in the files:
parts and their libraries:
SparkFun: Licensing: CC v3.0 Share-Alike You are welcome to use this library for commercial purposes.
